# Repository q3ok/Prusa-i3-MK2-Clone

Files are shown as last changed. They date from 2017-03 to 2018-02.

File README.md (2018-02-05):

# MK2 Clone - 3D Printer

If you are looking for current one - MK2Clone r2, follow this link:
https://github.com/q3ok/Prusa-i3-MK2-Clone/tree/r2

If you are looking for the first, older one - r1, follow this link:
https://github.com/q3ok/Prusa-i3-MK2-Clone/tree/r1

##### More informations
https://prusaclone.wordpress.com/

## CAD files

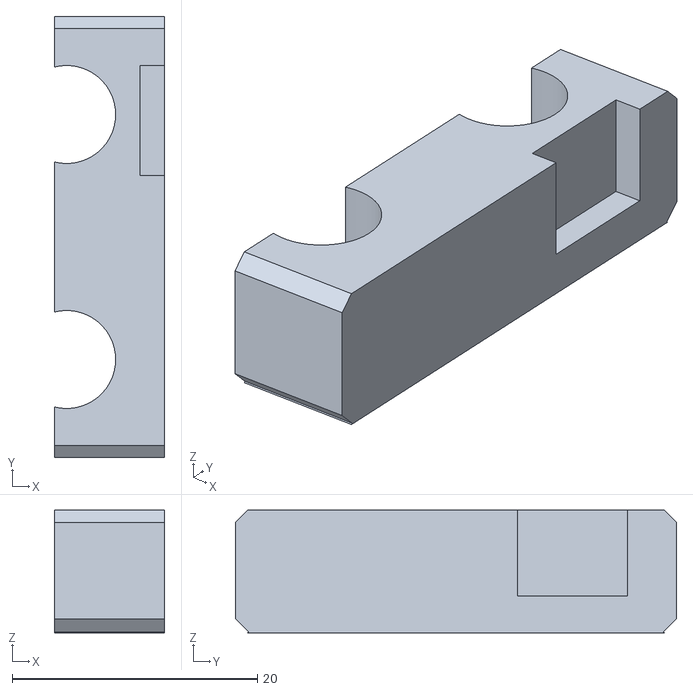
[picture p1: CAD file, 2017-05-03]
Printed-Parts/Optional/Y-motor-distance.stl
9.00 x 36.0 x 10.0

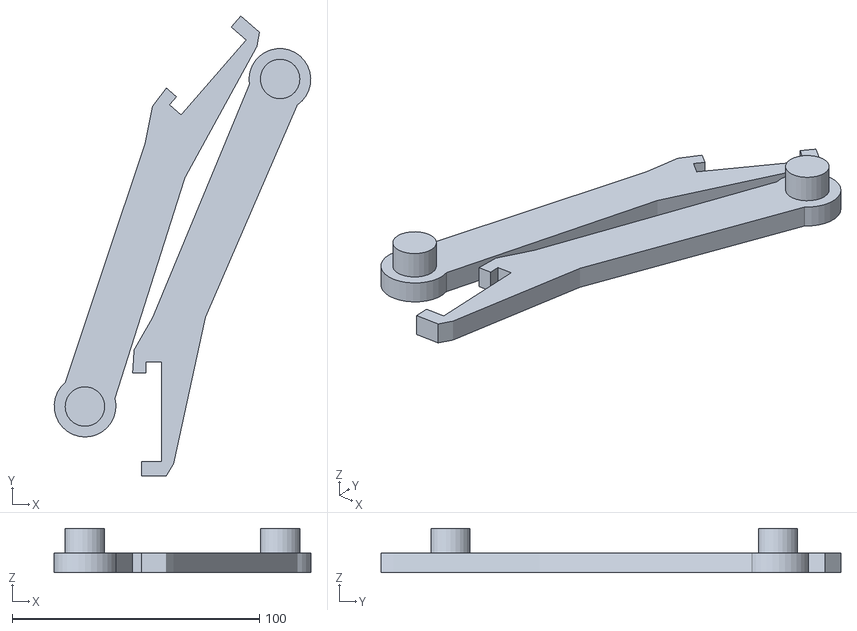
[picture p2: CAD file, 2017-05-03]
Printed-Parts/Spool holders/spool_holdahMK3_for_6mm_frame.stl
103.7 x 186.0 x 17.9

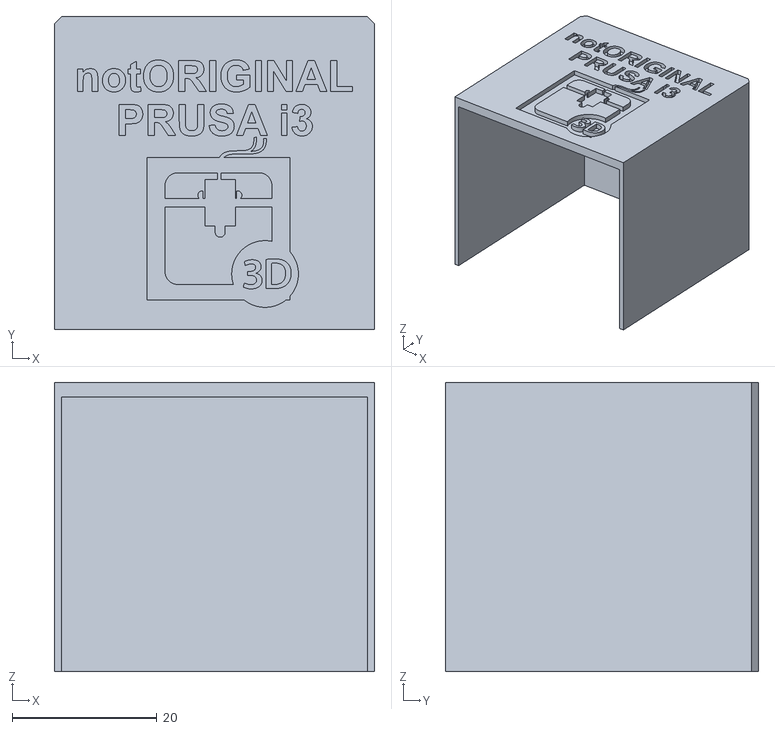
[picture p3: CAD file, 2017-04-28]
Printed-Parts/Optional/extruder-motor-cover-notORIGINAL.stl
44.3 x 43.3 x 40.0

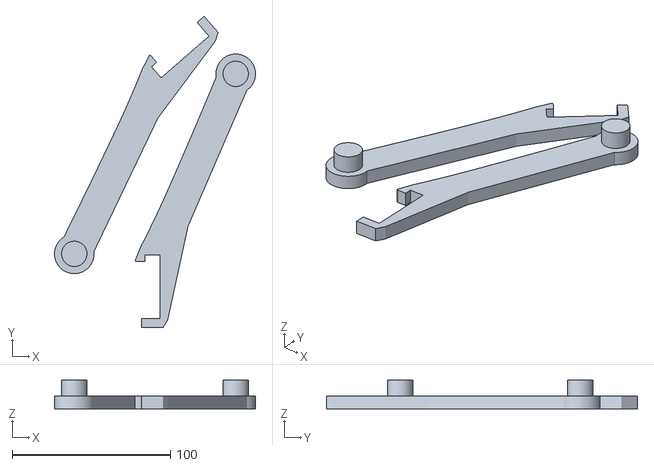
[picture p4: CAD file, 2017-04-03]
Printed-Parts/Spool holders/spool_holdahMK3_for_9mm_frame.stl
126.9 x 196.7 x 18.0

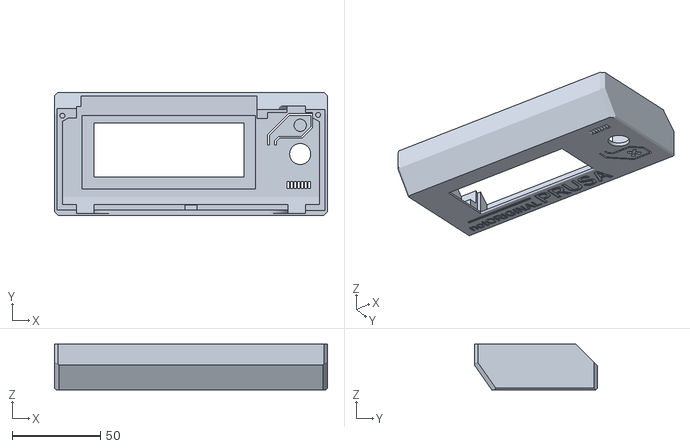
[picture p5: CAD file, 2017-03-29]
Printed-Parts/LCD-cover-notORIGINAL.stl
155.0 x 70.0 x 26.0

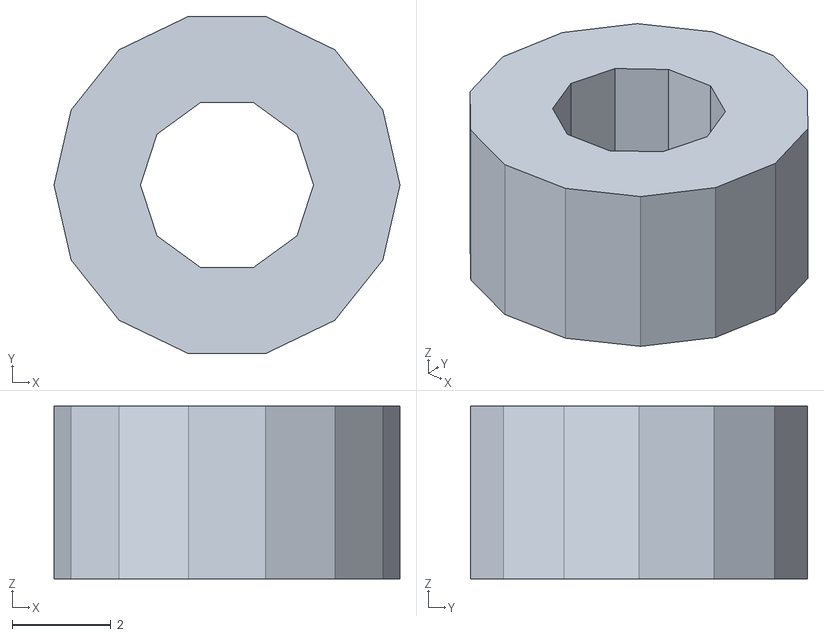
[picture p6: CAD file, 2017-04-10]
Printed-Parts/arduino-washer.stl
7.00 x 6.82 x 3.50

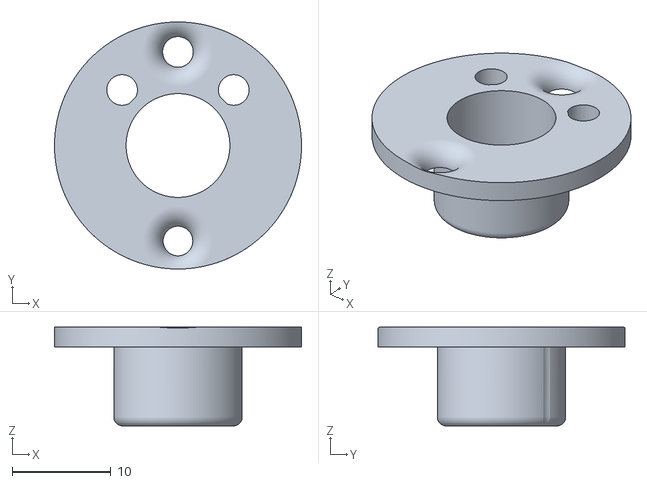
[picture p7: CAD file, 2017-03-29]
Printed-Parts/chinese_m8_nut_to_original_adapter.stl
25.0 x 25.0 x 10.0

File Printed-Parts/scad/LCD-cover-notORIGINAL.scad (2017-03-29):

// PRUSA iteration3
// LCD cover
// GNU GPL v3
// Josef Průša <iam@josefprusa.cz> and contributors
// http://www.reprap.org/wiki/Prusa_Mendel
// http://prusamendel.org


module main_body(){
difference() {
union() {
    // main body
    translate( [ -77 , -4.5 , 0 ] ) cube( [ 155 , 59.8 , 2 ] ); 
    translate( [ -77 , -4.5 , 0 ] ) rotate([35,0,0]) cube( [ 155 , 2 , 20.08 ] );
    translate( [ -77 , -14.7 , 14.2 ] )  cube( [ 155 , 2 , 11.8 ] );
    translate( [ -77 , 54 , 0 ] ) cube( [ 155 , 2 , 17 ] );
    
    // M3 hole body
    translate( [ 73.5 , 43.3 , 0.5 ] ) rotate([0,0,90])  cylinder( h = 14, r = 4, $fn=6);  
    translate( [ -72.5 , 43.5 , 0.5 ] ) rotate([0,0,90])  cylinder( h = 14, r = 4, $fn=6);  
    
}
translate( [ -61.5 , 1 , 1.2 ] ) cube( [ 98.5 , 42 , 10 ] );  // LCD window
translate( [ -54.5 , 8 , -1 ] ) cube( [ 85 , 30.5 , 10 ] );  // LCD window


// buzzer holes
translate( [ 55 , 1.5 , -1 ] ) cube( [ 1.3 , 4 , 10 ] );  
translate( [ 57 , 1.5 , -1 ] ) cube( [ 1.3 , 4 , 10 ] );  
translate( [ 59 , 1.5 , -1 ] ) cube( [ 1.3 , 4 , 10 ] );  
translate( [ 61 , 1.5 , -1 ] ) cube( [ 1.3 , 4 , 10 ] );  
translate( [ 63 , 1.5 , -1 ] ) cube( [ 1.3 , 4 , 10 ] );  
translate( [ 65 , 1.5 , -1 ] ) cube( [ 1.3 , 4 , 10 ] );  
translate( [ 67 , 1.5 , -1 ] ) cube( [ 1.3 , 4 , 10 ] );  

// buzzer holes corners
translate( [ 66.25 , 1.5 , -0.5 ] ) rotate([0,45,0]) cube( [ 2 , 4 , 2 ] );  
translate( [ 64.25 , 1.5 , -0.5 ] ) rotate([0,45,0]) cube( [ 2 , 4 , 2 ] );  
translate( [ 62.25 , 1.5 , -0.5 ] ) rotate([0,45,0]) cube( [ 2 , 4 , 2 ] );  
translate( [ 60.25 , 1.5 , -0.5 ] ) rotate([0,45,0]) cube( [ 2 , 4 , 2 ] );  
translate( [ 58.25 , 1.5 , -0.5 ] ) rotate([0,45,0]) cube( [ 2 , 4 , 2 ] );  
translate( [ 56.25 , 1.5 , -0.5 ] ) rotate([0,45,0]) cube( [ 2 , 4 , 2 ] );  
translate( [ 54.25 , 1.5 , -0.5 ] ) rotate([0,45,0]) cube( [ 2 , 4 , 2 ] );  

// knob hole
translate( [ 62.5 , 21 , -1 ] ) cylinder( h = 10, r = 6, $fn=30);
translate( [ 62.5 , 21 , -1.2 ] ) cylinder( h = 2, r1 = 7, r2 = 6, $fn=30);

// reset button cutout
translate( [ 44 , 26 , -1 ] ) cube( [ 1 , 6 , 9 ] );  
translate( [ 48 , 26 , -1 ] ) cube( [ 1 , 2.5 , 9 ] );  
translate( [ 68.5 , 36 , -1 ] ) cube( [ 1 , 8 , 9 ] );  
translate( [ 56 , 43 , -1 ] ) cube( [ 13.5 , 1 , 9 ] ); 
translate( [ 50.5 , 30 , -1 ] ) cube( [ 13 , 1 , 9 ] ); 
translate( [ 44.7 , 31.28 , -1 ] ) rotate([0,0,45]) cube( [ 17 , 1 , 9 ] );  
translate( [ 63.5 , 30 , -1 ] ) rotate([0,0,45]) cube( [ 8.5 , 1 , 9 ] );  
translate( [ 48.7 , 27.8 , -1 ] ) rotate([0,0,45]) cube( [ 3.55 , 1 , 9 ] );

// rear support cutout
translate( [ -64.5 , -12.7 , 14 ] ) cube( [ 10 , 3 , 16 ] );  
translate( [ 55.5 , -12.7 , 14 ] ) cube( [ 10 , 3 , 16 ] );  

}
}

module pcb_clip(){
    difference(){
    union(){
    translate( [ -3 , -12 , 17.5 ] ) cube( [ 7 , 4 , 5 ] ); 
    /* support removed */
    //translate( [ -3 , -10.6 , 12.5 ] ) cube( [ 1 , 2.6 , 7 ] );  
    //translate( [ 3 , -10.6 , 12.5 ] ) cube( [ 1 , 2.6 , 7 ] );  
        }
    translate( [ -4 , -8 , 18.5 ] ) rotate([30,0,0]) cube( [ 10 , 6 , 6 ] );  
   
    translate( [ 2.5 , -12 , 14.5 ] ) cube( [ 1 , 4 , 0.2 ] );  
    translate( [ -2.5 , -12 , 14.5 ] ) cube( [ 1 , 4 , 0.2 ] );  
    translate( [ 2.5 , -12 , 17.3 ] ) cube( [ 1 , 4 , 0.2 ] );  
    translate( [ -2.5 , -12 , 17.3 ] ) cube( [ 1 , 4 , 0.2 ] );          
}
}



difference()
{
union()
{

pcb_clip();

main_body();
// reset button
translate( [ 62.5 , 37.3 , 0 ] ) cylinder( h = 7.2, r = 3.5, $fn=30); 

//left side
translate( [ -77 , -14.7 , 0 ] ) cube( [ 1.5 , 70.7 , 26 ] );  
translate( [ -76.5 , -15 , 0 ] ) cube( [ 4 , 70 , 14.6 ] );  

//right side
translate( [ 76.5 , -14.7 , 0 ] ) cube( [ 1.5 , 70.7 , 26 ] ); 
translate( [ 73.5 , -14 , 0 ] ) cube( [ 4 , 70 , 14.5 ] );  

//rear side reinforcement
translate( [ -54.5 , -11.7 , 8 ] ) cube( [ 110 , 4 , 6.5 ] );  
translate( [ 65.5 , -11.7 , 8 ] ) cube( [ 12 , 4 , 6.5 ] );  
translate( [ 65.5 , -13 , 14 ] ) cube( [ 12 , 2 , 12 ] );  
translate( [ -76.5 , -11.7 , 8 ] ) cube( [ 12 , 4 , 6.5 ] );  
translate( [ -76.5 , -14.7 , 14.5 ] ) cube( [ 12 , 4 , 11.5 ] );  
translate( [ -44 , -14.7 , 14.5 ] ) cube( [ 89 , 4 , 11.5 ] );  
translate( [ -43.5 , -10.7 , 15 ] ) rotate([90,0,0]) cylinder( h = 2, r = 11, $fn=60);  
translate( [ 44.5 , -10.7 , 15 ] ) rotate([90,0,0]) cylinder( h = 2, r = 11, $fn=60);  


//front left side reinforcement
difference()
{
    union(){
        translate( [ -77 , 41.3 , 0 ] ) cube( [ 15 , 14 , 25 ] );  
        translate( [ -77 , 46.3 , 14 ] ) cube( [ 15 , 9 , 3 ] );  
        }
    translate( [ -64.5 , 40 , -3 ] ) cube( [ 4 , 8 , 40 ] );  
    translate( [ -75.5 , 40.3 , 14.5 ] ) cube( [15 , 6.5 , 25 ] ); 
}


//front right side reinforcement
difference(){
translate( [ 38 , 41.2 , 0 ] ) cube( [ 40 , 14 , 26 ] );  
translate( [ 55 , 44.5 , 0 ] ) cube( [ 10.5 , 3.7 , 30 ] );  
translate( [ 44 , 39.5 , 0 ] ) cube( [ 25.5 , 5 , 30 ] );  
translate( [ 35 , 39.3 , 14.5 ] ) cube( [ 42.5 , 7 , 15 ] );  

translate( [ 49 , 43.2 , 25 ] ) rotate([0,60,0]) cube( [ 12 , 5 , 10 ] );  
    

}
}

// SD card opening
translate( [ -80 , 9 , 14.5 ] ) cube( [ 10 , 28 , 6 ] );  

// front and rear angle
translate( [ -81 , -9.3 , -17 ] ) rotate([35,0,0]) cube( [ 164 , 14 , 54.08 ] );  
translate( [ -78 , 72.7 , -3 ] ) rotate([45,0,0]) cube( [ 160 , 14 , 54.08 ] );  

// M3 screw thread
translate( [ 72.7 , 43.2 , 3 ] ) cylinder( h = 20, r = 1.4, $fn=30);  
translate( [ -72.5 , 42.7 , 3 ] ) cylinder( h = 20, r = 1.4, $fn=30); 
translate( [ 72.7 , 43.2 , 14 ] ) cylinder( h = 1, r1 = 1.4, r2=2, $fn=30);  
translate( [ -72.5 , 42.7 , 14 ] ) cylinder( h = 1, r = 1.4, r2=2, $fn=30); 


// ORIGINAL PRUSA text
translate([-71,52,0.6]) rotate([180,0,0]) linear_extrude(height = 2) 
{ text("notORIGINAL",font = "helvetica:style=Bold", size=6, center=true); }

translate([-18,52,0.6]) rotate([180,0,0]) linear_extrude(height = 2) 
{ text("PRUSA",font = "helvetica:style=Bold", size=11, center=true); }

translate( [ -66 , 41.5 , -0.4 ] )  cube( [ 45 , 1.6 , 1 ] );  
translate( [ -66 , 42.3 , -0.4 ] ) cylinder( h = 1, r = 0.8, $fn=30);  
translate( [ -21 , 42.3 , -0.4 ] ) cylinder( h = 1, r = 0.8, $fn=30);  

// front cleanup
translate( [ -100 , -64 , 0 ] ) cube( [ 200 , 50 , 50 ] ); 

// X sign on reset button
translate( [ 63 , 34 , -1 ] ) rotate([0,0,45]) cube( [ 2, 8, 2 ] );  
translate( [ 57.5 , 35.5 , -1 ] ) rotate([0,0,-45]) cube( [ 2, 8, 2 ] );  


// corners
translate( [ 76 , -5 , -1 ] ) rotate([0,45,0]) cube( [ 5, 80, 5 ] );  
translate( [ -82 , -5 , -1 ] ) rotate([0,45,0]) cube( [ 5, 80, 5 ] );  
translate( [ -82 , 58 , -4 ] ) rotate([45,0,0]) cube( [ 200, 5, 5 ] );  
translate( [ -77 , 54 , -4 ] ) rotate([0,0,45]) cube( [ 5, 5, 50 ] );  
translate( [ 78 , 54 , -4 ] ) rotate([0,0,45]) cube( [ 5, 5, 50 ] );  
translate( [ 78 , -19 , -4 ] ) rotate([0,0,45]) cube( [ 5, 5, 50 ] );  
translate( [ -77 , -19 , -4 ] ) rotate([0,0,45]) cube( [ 5, 5, 50 ] );  

// LCD corners
translate( [ -54.5 , 9.5 , -5.2 ] ) rotate([45,0,0]) cube( [ 85 , 5 , 5 ] );  // LCD window
translate( [ -54.5 , 37 , -5.2 ] ) rotate([45,0,0]) cube( [ 85 , 5 , 5 ] );  // LCD window

rotate([35,0,0]) translate( [ -78 , -7 , -4 ] ) rotate([0,0,45]) cube( [ 5, 5, 50 ] );  
rotate([35,0,0]) translate( [ 79 , -7 , -4 ] ) rotate([0,0,45]) cube( [ 5, 5, 50 ] );  

}

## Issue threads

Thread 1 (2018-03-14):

Are the STL files updated to the corrct ones?

Pepetruen0, 2018-03-14:
I saw there were problems with the X axis parts being misaligned and something about the extruder gear. Are these issues corrected and can I print all the parts from this branch or should I pick and match from the r2 branch?

q3ok, 2018-03-18:
Position of the belt in x-carriage using x-end-idler and GT2-16 idler makes it a little bit misaligned, it's same case for Y axis. If you will choose GT2-20 idlers instead of 16, the x-ends will be ok.
extruder-body has one hole moved a little bit, and the x-carriage should have this modification too, however it will work.
The MK2Clone r2 doesn't have mechanical endstops, thus the modified parts cannot be used 1:1.

cyberhasse, 2018-06-28:
Hi!
The lcd-cover files seems to be openscad files instead of stl but i can't
open them in openscad..
Regards.

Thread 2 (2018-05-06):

Potential alternative to LJ8A3-4-Z/BX-5V inductive sensor

nweller922, 2018-05-06:
Would the LJ12A3-4-Z/BX-5V, which can be easily found online, work as a stand-in for the LJ8A3-4-Z/BX-5V sensor recommended in the guide? It appears the threading is the only difference.

Would it just require a modification of the printed parts? And if so, which one(s)?

nweller922, 2018-05-09:
Solution: The LJ12A3 sensor should work, but will require the use of a different version of extruder-body.stl. A suitable replacement can be found at https://www.thingiverse.com/thing:2261050

Closed 2018-05-09.

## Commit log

2017-03-29 LCD Cover notORIGINAL
    LCD Cover parts with notORIGINAL text
    [LCD-cover-notORIGINAL.scad, LCD-cover-notORIGINAL.stl]
2017-03-29 Adapter for chinese m8 trapezoidal nut
    [chinese_m8_nut_to_original_adapter.stl]
2017-04-03 Configuration file for Marlin RC8
    [Configuration.h]
2017-04-03 Spool holder STL modified for 9mm width frame
    [spool_hooldah_mk3_for_9mm_plywood.stl]
2017-04-10 Modified the configuration and added arduino washer
    [Configuration.h, arduino-washer.stl]
2017-04-28 Updated configuration and added extruder motor cover
    [Configuration.h, Configuration_adv.h, extruder-motor-cover-notORIGINAL.stl]
2017-05-03 Modifications
    Added all required files as stl
    Added bill of materials
    Reorganized folder structure
    Removed configuration for marlin, provided link to firmware
    Modified lcd-support
    [Configuration.h, Configuration_adv.h, LCD-cover-notORIGINAL.scad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]
2017-05-04 Updated Y-Corner to version from MK2S
    [y-corners.stl]
2017-11-19 updated x-end-idler and x-end-motor
    [bearing.scad, polyholes.scad, skewed_x-end-idler.stl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]
2017-12-26 Marlin configuration, removed BOM, modified readme
    [Configuration.h, Configuration_adv.h]
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2018-01-06 marlin config changes
    - changes max feedrate for E1
    - enabled multiple probing, set to 3,
    - decreased clearance between z probes
    - changed bed size (to 214x214)
    - modified x_min_pos
    - disabled maximum software endstops
    - decreased bumps while homing
    - increased manual feedrate for Z and decreased for E
    - enabled sd card sorting
    - enabled abort on endstop
    - enabled zprobe offset with babystepping connection
    - enabled linear advance
    [Configuration.h, Configuration_adv.h]
2018-01-06 New fan nozzle
    Changed fan nozzle to a better one made by R0b0Genius
    [fan-nozzle.stl]
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2018-01-06 Modified fan-nozzle
    - added "HOT" on front of the fan-nozzle
    [fan-nozzle.stl]
2018-01-09 Repository clear, preparation for r2
    [LCD-cover-notORIGINAL.stl, extruder-motor-cover-notORIGINAL.stl, spool-holder.stl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]
2018-01-09 Fined extruder body and x-carriage
    - as chinese inductive sensor is longer than pinda - modified the cale management to run the cables higher than in original
    - hole for left upper nema17 screw was misaligned on x-carriage, as the body with mk8 had the motor moved by 1mm left, now its in line
    - made the holes for nuts to screw the inductive sensor bigger (to fit also the hexagot nuts)
    - made more space for cables from 3030 hotend fan (a little bit more), experimental
    [extruder-body.stl, x-carriage.stl]
2018-01-10 x-carriage refinement
    - modified belt guide in carriage to be straight to x-end-idler
    - made endstop "clicker" larger (bigger)
    - decreased the heater cables holder to avoid collisions with frame and frame screws
    [x-carriage.stl]
2018-01-10 Refinements of STLs
    - Added lcd custom cover, knob and cable clip
    - Refined y-belt-holder (beta)
    [lcd-cable-clip.stl, lcd-cover.scad, lcd-cover.stl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]
2018-01-12 refinement of y-axis front and rear
    - modifications to y-axis front and y-axis rear to allow more easy print without any supports
    [y-axis-front.stl, y-axis-rear.stl]
2018-01-13 added y-rear-spacer and modified lcd-knob
    - added y-rear-spacer to make assembly of this printer more easy
    - modified lcd knob as it was too loose
    [lcd-knob.stl, y-rear-spacer.stl]
2018-01-14 Custom frame, modified readme
    - removed old vanilla frames
    - added new frame especially made for 10mm cutting from plywood
    - modified readme file
    [mk2clone-frame.dxf, mk2clone-r2-frame-10mm.dxf, prusai3-vanilla-alu-frame.dxf]
2018-01-15 Spool holder updated for 10mm
    - modified spool holder to fit on 10mm frame
    [spool-holder.stl]
2018-01-19 Updated configuration to use two stepper drivers for Z axis
    - as when using TMC its better to run every stepper motor on different
    stepstick, the configuration has been changed to use E1 stepper motor as
    second motor Z driver
    [Configuration_adv.h]
2018-01-20 Added cover for arduino + ramps (beta)
    [RAMPS_cover_bottom.stl, RAMPS_cover_side1.stl, RAMPS_cover_side2.stl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]
2018-01-20 Modified extruder, added bill of materials
    - Added place for optical sensor on extruder body
    - Modified extruder idler to still be able to work with the sensor on top of the extruder
    - added bill of materials (still work in progress)
    [extruder-body.stl, extruder-idler-rod.stl, extruder-idler.stl]
2018-01-21 Added power supply cover
    [power-supply-cover.stl]
2018-01-21 Removed RAMPS cover
    Removed the ramps cover until it will be modified
    [RAMPS_cover_bottom.stl, RAMPS_cover_side1.stl, RAMPS_cover_side2.stl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]
2018-01-21 Modified electronics cover
    - (beta) electronics cover from two parts - base and top
    [electronics-cover-base.stl, electronics-cover-top.stl]
2018-01-21 Refined extruder-body
    - enlarged two side holes for m3 nuts to fut
    - added additional filament guide in the big hole (highlt experimental)
    - removed top little part above place for filament sensor
    - added a chamber on the top hole for filament entrance
    [extruder-body.stl]
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2018-01-22 Updated fan nozzle and readme
    [fan-nozzle.stl]
2018-01-22 Updated bill of materials, refined electronics-cover
    [arduino-washer.stl, electronics-cover-base.stl, electronics-cover-top.stl]
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2018-01-24 Refined extruder-body filament sensor mount
    [extruder-body.stl]
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2018-01-25 Refinement of electronics cover-base and extruder-body
    - Removed the chamber of top of cover-base
    - Refinement of filament sensor fitting on extruder-body
    [electronics-cover-base.stl, extruder-body.stl]
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2018-01-27 Updated x-ends and electronics cover base
    - Refined x-ends which was remade by dulouie to fit bigger (higher) Tr8 chinese nut
    - Refined again the electronics cover (base)
    [electronics-cover-base.stl, x-end-idler.scad, x-end-idler.stl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]
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2018-02-05 Initial upload of custom marlin firmware (beta)
    - Added quick access to Z moves by doubleclick on status
    - Instant moves from menus
    - Added calibration menu with auto-UBL script and auto Z-adjust by moving to the top
    - Added Live Z adjustment on top of the main menu
    [Configuration.h, Configuration_adv.h]
2018-02-05 Made the master branch as "starter" page for the MK2Clone versions
    [Configuration.h, Configuration_adv.h, LCD-cover-notORIGINAL.stl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]
